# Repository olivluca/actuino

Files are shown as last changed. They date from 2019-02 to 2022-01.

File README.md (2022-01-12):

# Actuino
This is an arduino program, schematics and utilities to control an old stile linear or horizon to horizon actuator to steer a satellite dish.
This kind of actuator usually needs a 36V supply (I drive mine at 12V to reduce noise) and has a reed relay that gives pulses while the motor is running. By counting the pulses you know the position of the actuator (and the position of the dish).

A previous iteration used a parallel port and a Linux device driver, but since it's increasingly difficult to find a PC with a parallel port and there's an abundance of cheap TV boxes with usb ports,
I decided to write an arduino version controlled with an usb to serial cable.

I've been using it with a tv box running kodi and tvheadend (the trunk version of tvheadend can use an external command to move the dish), but since the tv box died now I'm using it with an enigma2 box running [openatv](https://github.com/openatv/enigma2/commit/8ad64e488b32b3b1896f9dddfaf1278edb525406).

# Components

* an arduino pro mini (atmega 168, but you can use another model)
* a 2 relays module,
* an usb to ttl adapter (to power the arduino and the relays)
* an fram chip FUJITSU MB85RC04V to store the satellite position
* an optocoupler to decouple the reed sensor from the arduino

# Schematics
I made the schematics in Fritzing (the file actuino.fzz).
I also provide a png rendering of the [breadboard view](actuino_bb.png) and [schematics view](actuino_schem.png) .

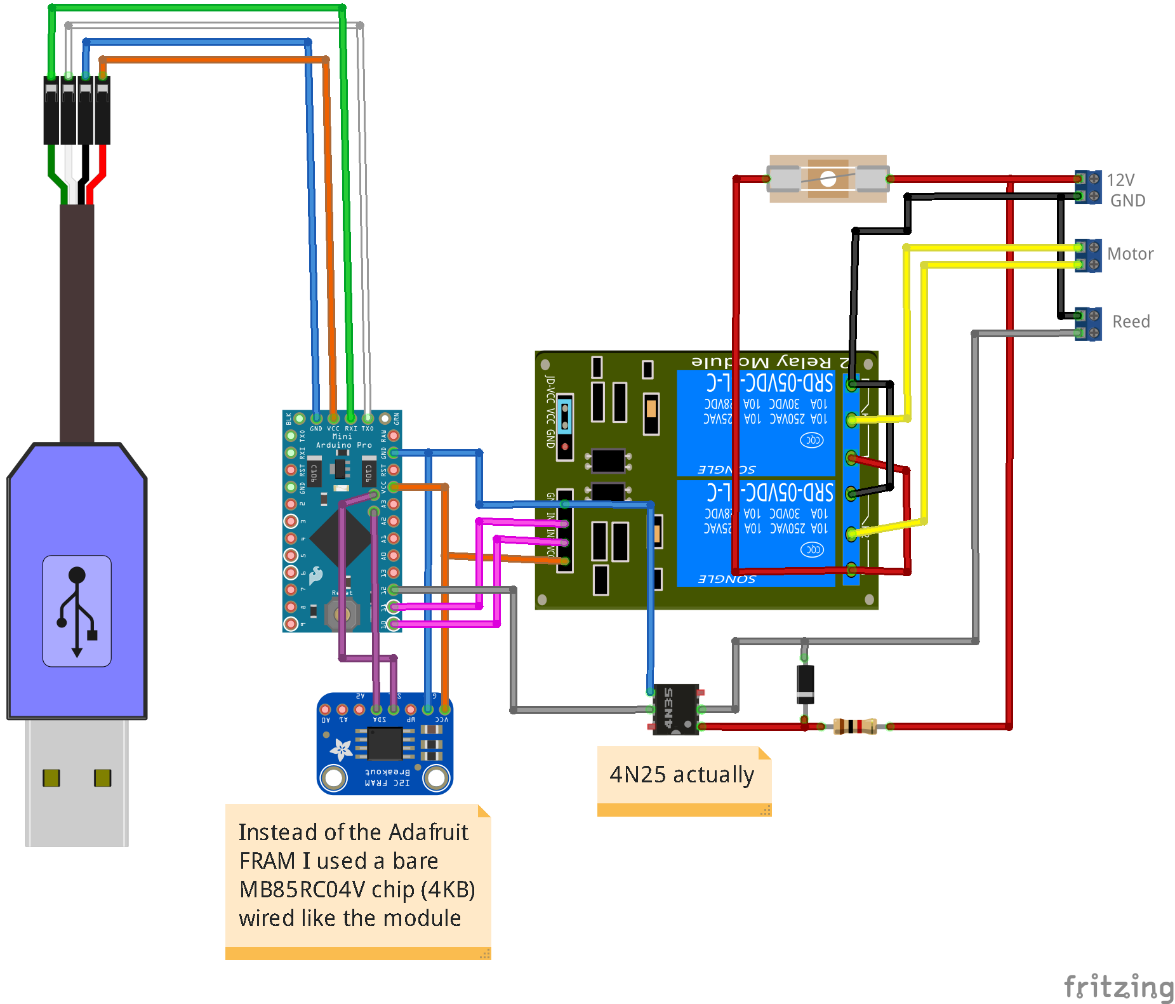
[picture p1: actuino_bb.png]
breadboard view
 

# Arduino program

In order to avoid burning the internal EEPROM, I use an FRAM chip to keep the current position of the dish. 
The chip is connected using I2C and I'm using the I2C-Master-Library, however I had to fork it in order to add functions to identify the chip.
My forked version is available on [github](https://github.com/olivluca/I2C-Master-Library).

I decided that the count increases when the dish moves west and decreases when it moves east.

## Commands

Usually you'll use the provided utilities to move the dish, but for debugging purposes you can send commands directly with a terminal program (though you'll have to type them quickly since the arduino will time out otherwise).
The commands are a single character, some of the commands need a parameter. There is no space between the command and the parameter. The commands are terminated with CR or LF.

The available commands are:

* **H**  stops the motor
* **D** disables the software limits
* **E** enables the software limits
* **\-** stores the actual position as the east limit
* **\+** stores the actual position as the west limit
* **<** *parameter* moves the dish east. A positive parameters specifies the number of steps the dish has to move, while a negative parameter specifies the duration of the movements in ms
* **\>** *parameter* moves the dish west. Like < it accepts a positive or negative number as a parameter.
* **G** *parameter* moves the dish to the specified position
* **?** shows the current status (see below)
* **X**  clears the internal EEPROM (which only stores the limits)
* **P** *parameter* sets the current position

## Status

The status returned by ? is a line with various fields separated with commas. The format of the line is

**status code,error code,target,position,east limit,west limit,limits enabled,free ram**

The status code is 0 with the dish stopped, 1 when moving west and 2 when moving east.
The possible error codes are:

* 0 no error
* 1 position lost (could be a faulty fram or a write operation interrupted by a power loss)
* 2 east limit reached
* 3 west limit reached
* 4 dish not moving (no pulses from the reed switch)

# Utilities

These are some python scripts useful for controlling the dish:

* **sermux.py** multiplexes the serial port to multiple tcp connections
* **manual.py** allows to move the dish manually with a curses interface

## sermux.py

Since only one program at a time can open the serial port, this script keeps the port open and allows other programs to control the actuator through
a TCP connection.
This way multiple programs can control the actuator at the same time (though care should be taken to avoid conflicting movements).
It also sends status messages to the running enigma2 instance at localhost to give some feedback about the dish movement.
By default it listens on tcp port 12345, but you can specify a different port with the --port parameter.
It should be left running all the time.

## manual.py

This program provides a curses interface to control the dish. It connects to the host specified as its parameter, port 12345. It gives a list
of the available options and shows the current status of the actuator.
Also, it allows to lock the serial port to avoid other clients to move the dish (they can still check the status).

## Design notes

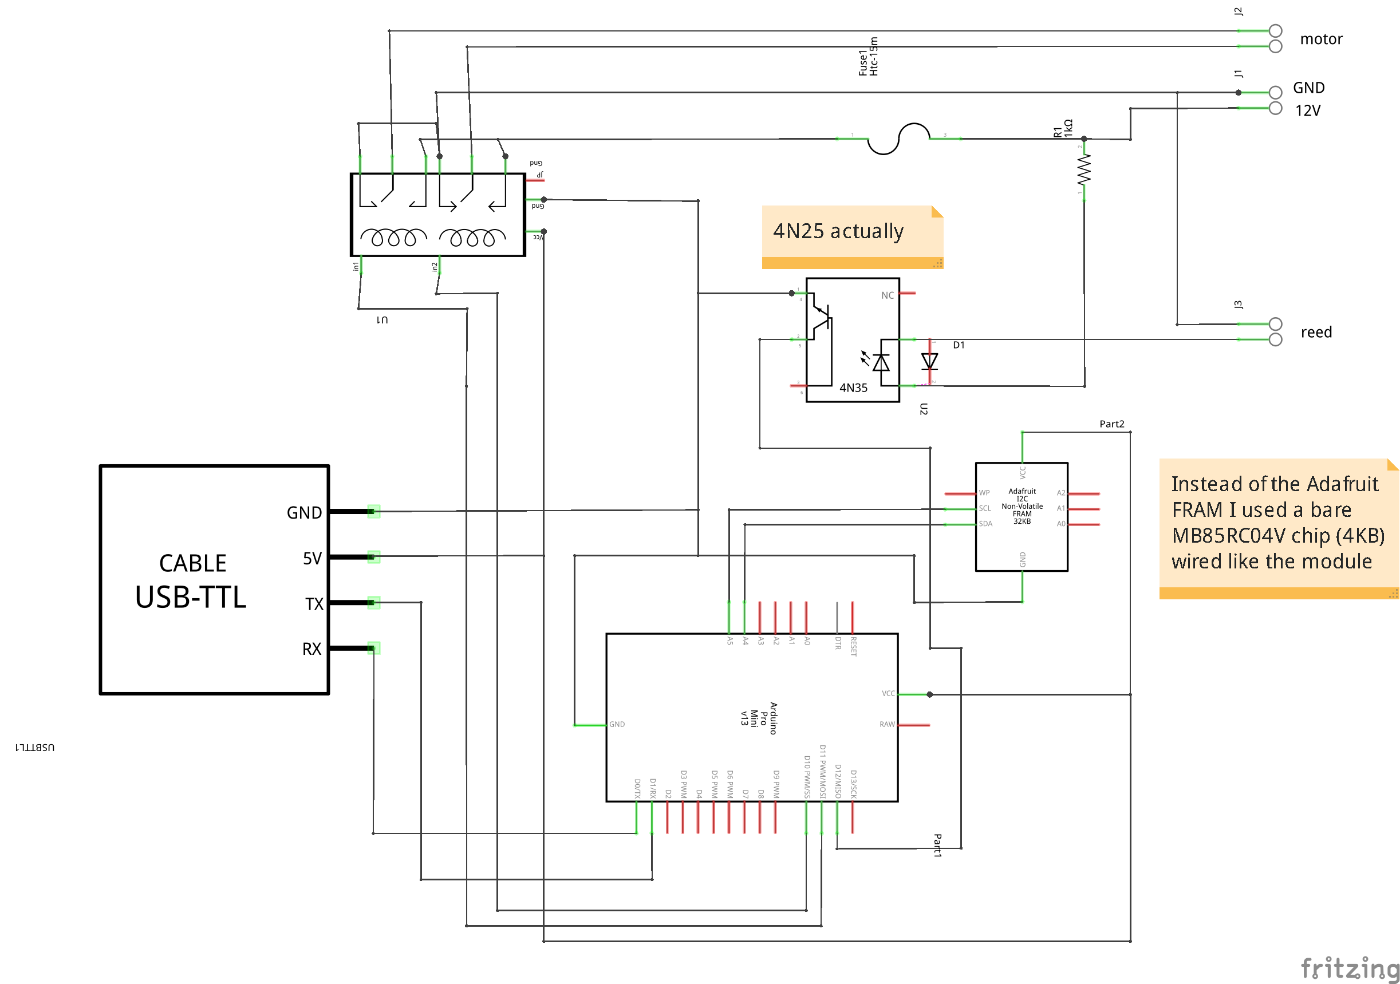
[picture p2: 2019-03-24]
actuino_schem.png

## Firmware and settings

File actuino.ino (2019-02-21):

#include <I2C.h>
#include <avr/eeprom.h>
#include <avr/pgmspace.h>
#include <stdlib.h>
#include "motor.h"

#define GO_WEST 10
#define GO_EAST 11
#define REED 12 
#define LED 13

#define CMD_HALT             'H'
#define CMD_DISABLE_LIMITS   'D'
#define CMD_ENABLE_LIMITS    'E'
#define CMD_SET_EAST_LIMIT   '-'
#define CMD_SET_WEST_LIMIT   '+'
#define CMD_GO_EAST          '<'
#define CMD_GO_WEST          '>'
#define CMD_GO_POSITION      'G'
#define CMD_SHOW_STATUS      '?'
#define CMD_FORMAT           'X'
#define CMD_SET_POSITION     'P'


enum errors {
  ERR_NOERROR=0,
  ERR_LOST_POS,
  ERR_LIMIT_EAST,
  ERR_LIMIT_WEST,
  ERR_NOT_MOVING
};  

enum statuses {
  STS_STOPPED,
  STS_MOVING_WEST,
  STS_MOVING_EAST
};


enum params {
  limit_east,
  limit_west,
};

Motor motor(GO_WEST,GO_EAST,LOW);
int16_t target;
int16_t position;
int16_t param[limit_west+1];

byte write_sequence;

bool limits_enabled;
bool positioning;
bool reached;
errors error;

unsigned int timeout;
unsigned int halt_timer;

char recvbuffer[32];
int recvcount;
unsigned long recvtime;
unsigned long blink;

#define FRAM_ADDRESS (0x50)
#define SLAVE_ID (0xF8)

bool recv()
{
    char c;
    while (Serial.available()) {
        c=Serial.read();
        if (c=='\r' || c=='\n') {
            if (recvcount>0) {
                recvbuffer[recvcount]=0;
                recvcount=0;
                return true;
            }
        } else {
            if (recvcount<30) { //leave one byte for the termination
                recvbuffer[recvcount++]=c;
                recvtime=millis();
            }
        }
    }
    if (recvcount>0) 
        if (millis()-recvtime>1000)
            recvcount=0;
    return false;    
}

void check_fram(void)
{
    uint8_t a[3];
    uint16_t manufacturerID = 0;
    uint16_t productID = 0;
    
    if (I2c.write(SLAVE_ID >> 1, FRAM_ADDRESS << 1, true)!=0) {
        Serial.println("check_fram - error I2c.write");
    } else   
    if (I2c.read(SLAVE_ID >> 1, 3, a)!=0) {
        Serial.println("check_fram - error I2c.read ");
    } else { 
      manufacturerID = (a[0] << 4) + (a[1]  >> 4);
      productID = ((a[1] & 0x0F) << 8) + a[2];
    }
    if (manufacturerID!=0x0a || productID!=0x10) {
        if (manufacturerID!=0x0a) {
            Serial.print(F("Wrong manufacturerID 0x"));
            Serial.println(manufacturerID, HEX);
        }
        if (productID!=0x10) {
            Serial.print(F("Wrong productID 0x"));
            Serial.println(productID, HEX);
        }
        while(true) {
         digitalWrite(LED, HIGH);
         delay(100);
         digitalWrite(LED, LOW);
         delay(100);
        }
    }
}

uint8_t write_fram(uint16_t address, uint8_t *data, uint8_t len)
{
  uint8_t addr=FRAM_ADDRESS;
  if (address>0xff)
    addr|=1;
  return I2c.write(addr, address & 0xff, data, len);  
}

uint8_t read_fram(uint16_t address, uint8_t *data, uint8_t len)
{
  uint8_t addr=FRAM_ADDRESS;
  if (address>0xff)
    addr|=1;
  return I2c.read(addr, address & 0xff, len, data);  
}

/* write sequence is written before and after the position to
 * detect power loss during writing
 */
void save_position(void)
{
  byte buffer[4];
  write_sequence++;
  if (write_sequence==0)
    write_sequence=1;
  buffer[0]=write_sequence;
  buffer[1]=position >> 8;
  buffer[2]=position & 0xff;
  buffer[3]=write_sequence;
  write_fram(0, buffer, sizeof(buffer));
}

void clear_position(void)
{
  byte buffer=0;
  write_fram(0,&buffer,sizeof(buffer));
  error=ERR_LOST_POS;
}

void read_position(void)
{
  byte buffer[4];
  error=ERR_LOST_POS;
  position=0;
  /* if write_sequence is the same the position is valid */
  if (read_fram(0, buffer, sizeof(buffer))==0 && buffer[0]!=0 && buffer[0]==buffer[3]) {
    write_sequence=buffer[0];
    position=buffer[1] << 8 | buffer[2];
    error=ERR_NOERROR;
  }
}

#define OFFSET_PARAMS 4

void check_and_format_eeprom(void)
{
  union {
    char chars[4];
    uint32_t num;
  }  magic = { .chars = {'A','C','T','U'}};
  
  uint32_t readmagic;
  uint32_t readmagic2;
  uint32_t zero=0;
  unsigned int maxeprom=(OFFSET_PARAMS+sizeof(param));
  
  readmagic=eeprom_read_dword((uint32_t *)0);
  readmagic2=eeprom_read_dword((uint32_t *)maxeprom);
  if (magic.num==readmagic && magic.num==readmagic2)
    return;
  for (unsigned int i=4; i<maxeprom; i+=4) 
    eeprom_write_dword((uint32_t*) i, zero);
  eeprom_write_dword((uint32_t*)0, magic.num);  
  eeprom_write_dword((uint32_t*)maxeprom, magic.num);  
}

void save_param(int param_to_save) {
  eeprom_write_word((uint16_t*) (param_to_save*2+OFFSET_PARAMS), param[param_to_save]);
}

void read_params(void) {
  eeprom_read_block(&param, (void *) OFFSET_PARAMS, sizeof(param));
}

/* timeout between pulses */
void set_timeout(void)
{
  timeout=5000;
}

/* if no pulses are received while the motor is moving, stop the
 * motor and register the error
 */
void check_moving(void)
{
  if (!motor.Moving()) {
    set_timeout();
    return;
  }  
  if (--timeout)
    return;
  motor.Stop();
  positioning=false;
  //avoid clearing ERR_LOST_POS here
  if (error != ERR_LOST_POS)
    error=ERR_NOT_MOVING; 
}  

/* each ms */
SIGNAL(TIMER0_COMPA_vect)
{
  
  static int lastreed=HIGH;
  static unsigned int debounce=10;
  static int lastdebounced=HIGH;
  
  /* timer go east or go west */
  if (halt_timer!=0) {
    if (--halt_timer==0)
      motor.Stop();
  }
  /* read and debounce pulses */
  int reed=digitalRead(REED);
  if (reed==lastreed) {
     if (debounce) debounce--;
     else {  //debounced
        if (reed==LOW && reed!=lastdebounced) { //new pulse
            /* here we count pulses even with the position invalid to allow for 
             * manual movement, but don't save the position to fram
             */
            if (motor.LastDirection() == MD_WEST) { 
              position++;
              if (error != ERR_LOST_POS) {
                save_position();
                if (limits_enabled && position>=param[limit_west]) {
                  motor.Stop();
                  error=ERR_LIMIT_WEST;
                  positioning=false;
                }
              }  
            } else if (motor.LastDirection() == MD_EAST) {
              position--;
              if (error != ERR_LOST_POS) {
                save_position();
                if (limits_enabled && position<=param[limit_east])  {
                  motor.Stop();
                  error=ERR_LIMIT_EAST;
                  positioning=false;
                } 
              }  
            }  
            if (positioning && position == target) {
                motor.Stop();
                positioning=false;
                reached=true;
            }
            set_timeout(); 
        }
        lastdebounced=reed;  
     }
  } else {
    debounce=10;  
    lastreed=reed;
  }
  check_moving();
}

int freeRam () {
  extern int __heap_start, *__brkval;
  int v;
  return (int) &v - (__brkval == 0 ? (int) &__heap_start : (int) __brkval);
}

void setup()
{
  //Init i2c master library
  I2c.begin();

  I2c.setSpeed(true);
  // initialize the serial communication:
  Serial.begin(115200);
  Serial.setTimeout(100);
  // initialize the ledPin as an output:
  pinMode(REED, INPUT_PULLUP);
  pinMode(LED, OUTPUT);
  check_fram();
  check_and_format_eeprom();
  read_position(); //it will either set the error to ERR_NOERROR or ERR_LOST_POS
  read_params();
  limits_enabled=true;
  positioning=false;
  reached=false;
  halt_timer=0;
  blink = millis();
  
  //enable 1ms interrupt
  OCR0A = 0xAF;
  TIMSK0 |= _BV(OCIE0A);
}

byte getdisplaystatus(void) {
  if (!motor.Moving()) 
      return STS_STOPPED;
  if (motor.LastDirection()==MD_WEST)
   return STS_MOVING_WEST;
  return STS_MOVING_EAST;
}

void separator()
{
    Serial.write(',');
}
void show_status() 
{  
  Serial.print(getdisplaystatus()); separator();
  Serial.print(error); separator();
  Serial.print(target); separator();
  Serial.print(position); separator();
  Serial.print(param[limit_east]); separator();
  Serial.print(param[limit_west]); separator();
  Serial.print(limits_enabled); separator();
  Serial.println(freeRam());
}

void loop() {
  char command;
  int parameter;
      
  motor.Loop();
  
  command=0;
  
  //commands over serial
  if (recv()) 
  {
    command=recvbuffer[0];
    parameter=atoi(recvbuffer+1);
    switch (command) {
      case CMD_FORMAT:
        Serial.println(F("deleting magic and parameters"));
        eeprom_write_dword((uint32_t*)0, 0);  
        break;   

      case CMD_HALT:
        Serial.println(F("halt"));
        halt_timer=0;  
        motor.Stop();
        positioning=false;
        reached=false;
        if (error != ERR_LOST_POS)
          error=ERR_NOERROR;
        break;

      case CMD_DISABLE_LIMITS:
        limits_enabled=false;
        Serial.println(F("Limits disabled"));
        break;

      case CMD_ENABLE_LIMITS:
        limits_enabled=true;
        Serial.println(F("Limits enabled"));
        break;
        
      case CMD_SET_EAST_LIMIT: 
        if (error != ERR_LOST_POS) {
          param[limit_east]=position;
          save_param(limit_east);
          Serial.print(F("Set east limit "));
          Serial.println(param[limit_east]);
        } else {
          Serial.println(F("Limit not set (position lost)"));
        }
        break;

      case CMD_SET_WEST_LIMIT:
        if (error != ERR_LOST_POS) {
          param[limit_west]=position;
          save_param(limit_west);
          Serial.print(F("Set west limit "));
          Serial.println(param[limit_west]);
        } else {
          Serial.println(F("Limit not set (position lost)"));
        }
        break;

      case CMD_GO_EAST:
      case CMD_GO_WEST:
        bool go_west;
        go_west=command==CMD_GO_WEST;
        error=ERR_NOERROR;
        if (parameter>0) {
          target=position+parameter*( go_west ? 1 : -1);
          if (go_west && limits_enabled && target > param[limit_west])
            error=ERR_LIMIT_WEST;
          if (!go_west && limits_enabled && target < param[limit_east])
            error=ERR_LIMIT_EAST;
          if (error==ERR_NOERROR) {
            positioning=true;
            reached=false;
            halt_timer=0;
          }
        } else {
          if (go_west && limits_enabled && position>=param[limit_west])
              error=ERR_LIMIT_WEST;
          if (!go_west && limits_enabled && position<=param[limit_east])
              error=ERR_LIMIT_EAST;
          if (error==ERR_NOERROR) {
            halt_timer=-parameter;
            positioning=false;
          }
        }  
        if (error==ERR_NOERROR) {
          if (positioning) {
           Serial.print(parameter);
           Serial.print(F(" steps "));
          } else {
           Serial.print(-parameter);
           Serial.print(F(" ms "));
          }
          Serial.println(go_west ? F("west") : F("east"));
          motor.Go(go_west ? MD_WEST : MD_EAST);
        } else {
          motor.Stop();
          target=position;
          Serial.print(go_west ? F("West") : F("East"));
          Serial.println(F(" limit"));
        }
        break;

      case CMD_GO_POSITION:
        if (error != ERR_LOST_POS) {
          reached=false;
          error=ERR_NOERROR;
          if (limits_enabled && parameter<param[limit_east])
            error=ERR_LIMIT_EAST;
          else if (limits_enabled && parameter>param[limit_west])
            error=ERR_LIMIT_WEST;
          if (error==ERR_NOERROR)
          {
            positioning=true;
            halt_timer=0;
            target=parameter;
            if (target>position) motor.Go(MD_WEST);
            else if (target<position) motor.Go(MD_EAST);
            else {
              motor.Stop();
              positioning=false;
              reached=true;
             }
          }
        }
        show_status();
        break;

      case CMD_SET_POSITION:
        position=parameter;
        save_position();
        error=ERR_NOERROR;
        Serial.print(F("Position set to "));
        Serial.println(position);
        break;
        
      case CMD_SHOW_STATUS:
        show_status();
        break;
    }
  } //if recv()  
  
  if (error==ERR_NOERROR)
    digitalWrite(LED, HIGH);
  else {
      digitalWrite(LED, millis()-blink<250);
      if (millis()-blink>500)
        blink=millis();
  }
        
}

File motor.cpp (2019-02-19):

#include "motor.h"

Motor::Motor(int pinwest, int pineast, int active)
{
  m_pinwest=pinwest;
  m_pineast=pineast;
  m_active=active;
  digitalWrite(m_pinwest,!m_active);
  pinMode(m_pinwest, OUTPUT);
  digitalWrite(m_pineast,!m_active);
  pinMode(m_pineast, OUTPUT);
  lastdir=MD_STOP;
  stopped=true;
  m_lastwest=false;
  Stop();
}

void Motor::Stop()
{
  newdir=MD_STOP;
  /* the relay module I'm using is active with output low, high turns off the relays */
  digitalWrite(m_pinwest,!m_active);
  digitalWrite(m_pineast,!m_active);
  moving=false;
  if (!stopped) {
    //Serial.println("wait");
    stopped=true;
    wait=millis();
  }
}

void Motor::internalGo()
{
    /* the relay module I'm using is active with output low, high turns off the relays */
    digitalWrite(m_pinwest, lastdir==MD_WEST ? m_active : !m_active);
    digitalWrite(m_pineast, lastdir==MD_EAST ? m_active : !m_active);
    stopped=false;
    moving=lastdir!=MD_STOP;
    if (lastdir==MD_WEST)
      m_lastwest=true;
    if (lastdir==MD_EAST)
      m_lastwest=false;  
}

void Motor::Go(motor_direction dir)
{
  //Serial.print("motor go lastdir ");
  //Serial.print(lastdir);
  //Serial.print(" newdir ");
  //Serial.println(dir);
  if (dir!=lastdir && lastdir!=MD_STOP) {
    //Serial.println("Stop in go");
    Stop();
  }
  newdir=dir;
  if (newdir == lastdir || lastdir == MD_STOP) {
    //Serial.println("internalgo in go");
    lastdir=newdir;
    internalGo();
  } 
}

void Motor::Loop()
{
  if (lastdir!=MD_STOP && stopped) {
    if (millis()-wait>=1000) {
      lastdir=MD_STOP;
      //Serial.println("stopped");
    }  
  } 
  if (newdir!=MD_STOP && lastdir==MD_STOP) {
    lastdir=newdir;
    //Serial.println("internalgo in loop");
    internalGo();
  }
}

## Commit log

2019-03-24 schematics (made with fritzing)
    [actuino.fzz]
2019-03-24 added png renderings of the schematics
2019-03-24 README.md: added links to the schematics
2021-11-18 manual.py fixes for python3
    [manual.py]
2021-11-18 sermux.py python3 and enigma2 fixes
    [sermux.py]
2021-11-29 sermux.py only removes rotor_moving if position is close enough to target (to avoid considering the position reached when the dish is changing direction and stops before moving again)
    [sermux.py]
2021-11-29 sermux.py more python3 fixes
    [sermux.py]
